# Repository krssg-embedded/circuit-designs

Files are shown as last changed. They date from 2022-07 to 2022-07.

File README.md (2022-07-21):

# Circuit Design
This repo contains all the schematics and pcb layout designs relevant to the SSL bot.
There are three imporatant circuits in the bot:
1. Main Board
2. Kicker Circuit
3. Motor Driver

### Main Board

### Kicker Circuit
The kicker we use works on the principle of a solenoid.
The straight kicker is powered by two 250V 2200uF capacitors, which can be charged by a step-up converter to 200V each.
The kicker board constitutes of a charging and a discharging circuit. The FPGA on the main circuit is controlling the circuit. The board receives charge trigger and kicking level from the main circuit, charging the capacitor bank of 4400uF to 250V using flyback topology.
The charging circuit is based on LT3750, a flyback converter. It consists of a different resistor which can be used to change various output parameters like charging current. The CHARGE pin one the IC gives full control of the LT3750 to the user and the DONE pin indicates when the capacitor has reached its programmed value, and the part has stopped charging.
The capacitor is charged to its limit by using a boost convertor that steps up the voltage from the the 12V battery. The kicker is operated through a switch which disconnects the charging circuit and allows the charge from the capacitor to flow through the solenoid. 
As the kicker is made of a magnetic material as soon as the current flows the coil tries to bring as much of the kicker inside itself as possible. This is what generates the tremendous kicking force required to kick the ball.

### Motor Driver
MOTOR DRIVER
In motor driver, I learnt how to make a commutation table.
I learnt in detail about the internal circuitry of the driver. I read about power MOSFETs and their advantages. We were taught the problems that we currently face in running our BLDCs. I learnt to place the components on the PCB and solder them properly. I also read about the gate driver IC we use and how it helps us in switching the states of the mosfets.
I read about the various methods of sensing commutation which includes using Hall sensors, using encoders and finally back-EMF calculations. The methods of control like trapezoidal, sinusoidal and field oriented control. The current sensor IC ACS2590 was also introduced. 
The main takeaway was that there are problems in the circuitry that we use and many things can be improved like we can implement sinusoidal current by applying variable PWM or make the commutation smoother by adjusting the rise and fall time of the voltages at the gates.

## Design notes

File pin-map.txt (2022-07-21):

3 Hall sensor per wheel motor -> 12 pins total (Interrupt)
6 output per motor     	      -> 15 pins total (PWM) + 15 pins total (digital)
4 output per Kicker           -> 4 pins total (digtal)
NRF Radio Communication	      -> 5 pins total (SPI)
Infrared Sensors              -> 3 pins total (digital)   
SWDIO, SWCLK (Programming)    -> 2 pin total (Serial Wire Debug)
ACS712 Current Feedback       -> 5 pin total (Analog)
2 input Encoder per motor     -> 8 pin total (Interrupt)
----------------------------------------------------------------
			      == 69 pins overall :P

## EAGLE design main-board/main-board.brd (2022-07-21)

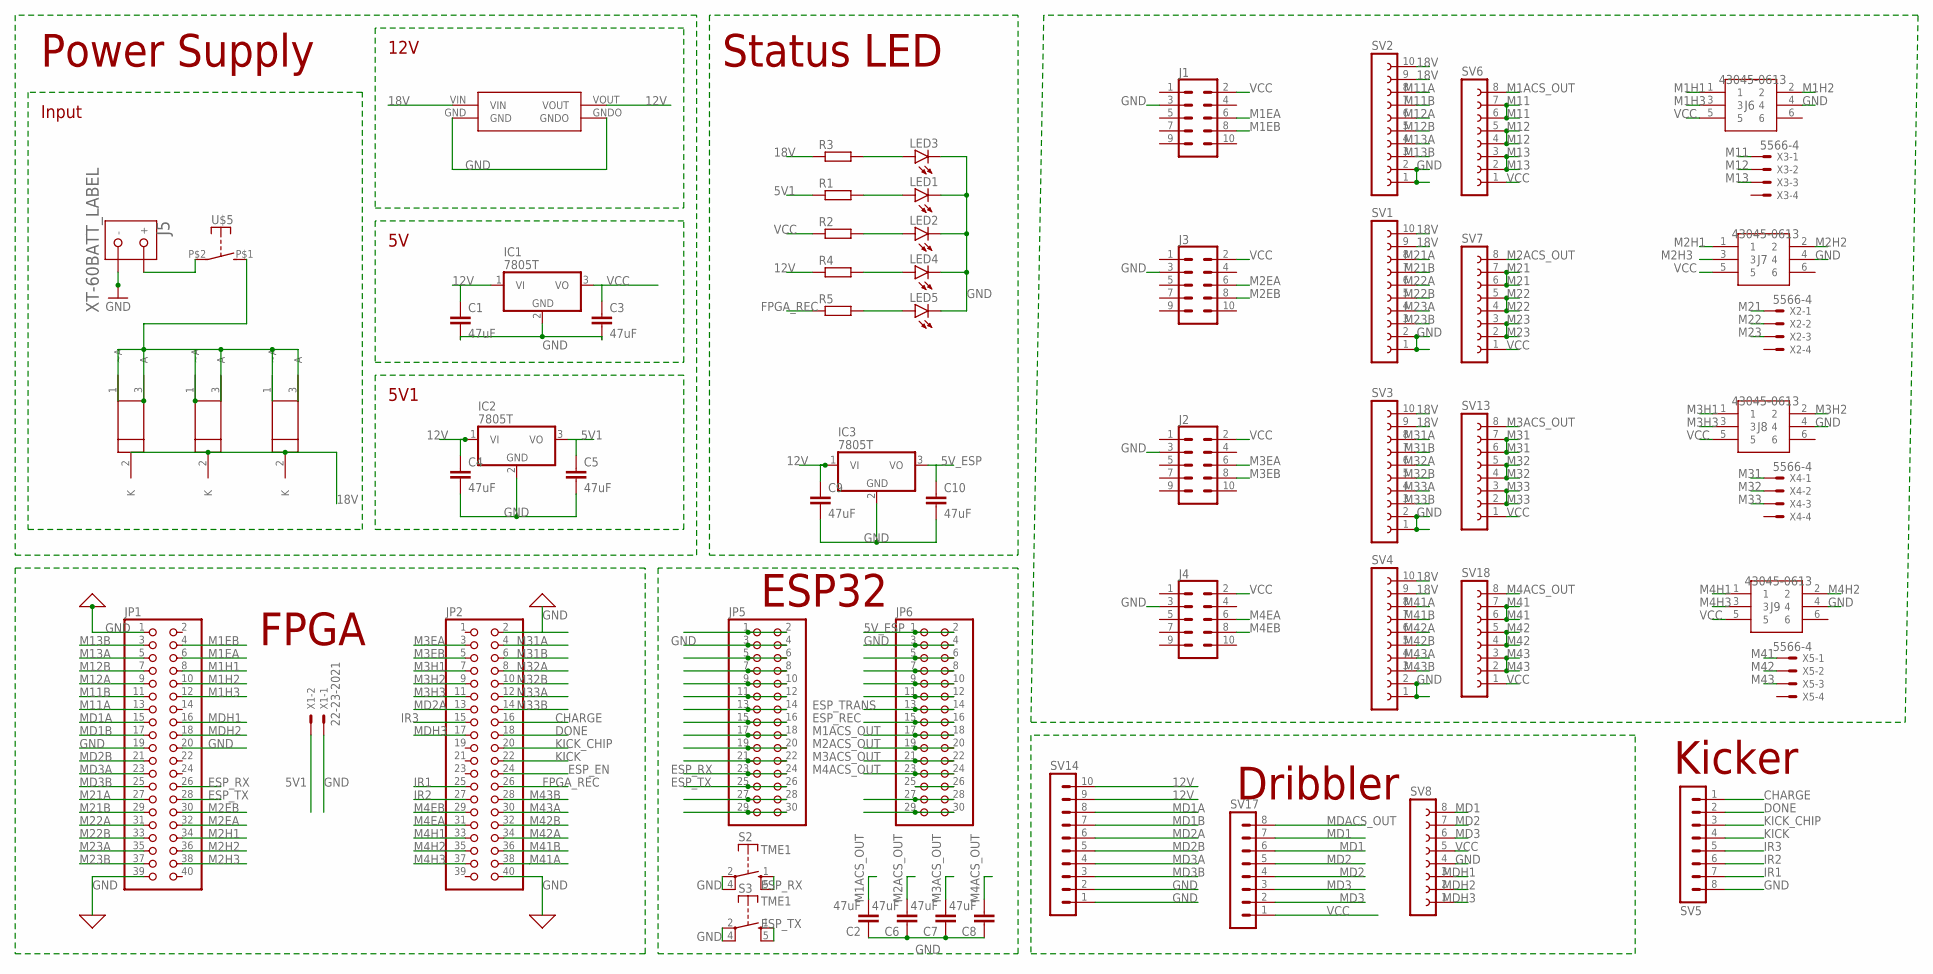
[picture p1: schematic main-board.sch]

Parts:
C1, C2, C3, C4, C5, C6, C7, C8, C9, C10: 47uF; C1206
IC1, IC2, IC3: 7805T; TO220H
J1, J2, J3, J4: CONN_05X2SHD_LOCK; 2X5-SHROUDED_LOCK
J5: XT-60BATT_LABEL; XT-60
J6, J7, J8, J9: 43045-0613
JP1, JP2: PINHD-2X20; 2X20
JP5, JP6: PINHD-2X15; 2X15
LED1, LED2, LED3, LED4, LED5: LEDSMT1206; 1206
R1, R2, R3, R4, R5: R-EU_R1206; R1206
S2, S3: TME1
SV1, SV2, SV3, SV4: FE10-1; FE10
SV5, SV17: MA08-1
SV6, SV7, SV8, SV13, SV18: FE08-1; FE08
SV14: MA10-1
U1, U2, U3: LP38690DT-3.3; TO228P1042X238-3N
U$4: BUCK
U$5: SWITCH_DA10; DA10
X1: 22-23-2021
X2, X3, X4, X5: 5566-4

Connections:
5V1: C5.1, IC2.3 (VO), R1.1, X1.2
5V_ESP: C10.1, IC3.3 (VO), JP6.1, JP6.2
12V: C1.1, C4.1, C9.1, IC1.1 (VI), IC2.1 (VI), IC3.1 (VI), R4.1, SV14.9, SV14.10, U$4.VOUT
18V: R3.1, SV1.9, SV1.10, SV2.9, SV2.10, SV3.9, SV3.10, SV4.9, SV4.10, U1.2 (K), U2.2 (K), U3.2 (K), U$4.VIN
CHARGE: JP2.16, SV5.1
DONE: JP2.18, SV5.2
ESP_EN: JP2.24
ESP_REC: JP6.15, JP6.16
ESP_RX: JP1.26, JP5.23, JP5.24, S2.1 (S), S2.5 (S)
ESP_TRANS: JP6.13, JP6.14
ESP_TX: JP1.28, JP5.25, JP5.26, S3.1 (S), S3.5 (S)
FPGA_REC: JP2.26, R5.1
GND: C1.2, C2.1, C3.2, C4.2, C5.2, C6.1, C7.1, C8.1, C9.2, C10.2, IC1.2 (GND), IC2.2 (GND), IC3.2 (GND), J1.3, J2.3, J3.3, J4.3, J5.GND (-), J6.4, J7.4, J8.4, J9.4, JP1.1, JP1.19, JP1.20, JP1.39, JP2.2, JP2.40, JP5.3, JP5.4, JP6.3, JP6.4, LED1.C, LED2.C, LED3.C, LED4.C, LED5.C, S2.2, S2.4, S3.2, S3.4, SV1.1, SV1.2, SV2.1, SV2.2, SV3.1, SV3.2, SV4.1, SV4.2, SV5.8, SV8.4, SV14.1, SV14.2, U$4.GND, U$4.GNDO, X1.1
INPUT: U1.1 (~A), U1.3 (A), U2.1 (~A), U2.3 (A), U3.1 (~A), U3.3 (A), U$5.P$1 (S)
IR1: JP2.25, SV5.7
IR2: JP2.27, SV5.6
IR3: JP2.15, SV5.5
KICK: JP2.22, SV5.4
KICK_CHIP: JP2.20, SV5.3
M1ACS_OUT: C2.2, JP6.17, JP6.18, SV6.8
M1EA: J1.6, JP1.6
M1EB: J1.8, JP1.4
M1H1: J6.1, JP1.8
M1H2: J6.2, JP1.10
M1H3: J6.3, JP1.12
M2ACS_OUT: C6.2, JP6.19, JP6.20, SV7.8
M2EA: J3.6, JP1.32
M2EB: J3.8, JP1.30
M2H1: J7.1, JP1.34
M2H2: J7.2, JP1.36
M2H3: J7.3, JP1.38
M3ACS_OUT: C7.2, JP6.21, JP6.22, SV13.8
M3EA: J2.6, JP2.3
M3EB: J2.8, JP2.5
M3H1: J8.1, JP2.7
M3H2: J8.2, JP2.9
M3H3: J8.3, JP2.11
M4ACS_OUT: C8.2, JP6.23, JP6.24, SV18.8
M4EA: J4.6, JP2.31
M4EB: J4.8, JP2.29
M4H1: J9.1, JP2.33
M4H2: J9.2, JP2.35
M4H3: J9.3, JP2.37
M11: SV6.6, SV6.7, X3.1
M11A: JP1.13, SV2.8
M11B: JP1.11, SV2.7
M12: SV6.4, SV6.5, X3.2
M12A: JP1.9, SV2.6
M12B: JP1.7, SV2.5
M13: SV6.2, SV6.3, X3.3
M13A: JP1.5, SV2.4
M13B: JP1.3, SV2.3
M21: SV7.6, SV7.7, X2.1
M21A: JP1.27, SV1.8
M21B: JP1.29, SV1.7
M22: SV7.4, SV7.5, X2.2
M22A: JP1.31, SV1.6
M22B: JP1.33, SV1.5
M23: SV7.2, SV7.3, X2.3
M23A: JP1.35, SV1.4
M23B: JP1.37, SV1.3
M31: SV13.6, SV13.7, X4.1
M31A: JP2.4, SV3.8
M31B: JP2.6, SV3.7
M32: SV13.4, SV13.5, X4.2
M32A: JP2.8, SV3.6
M32B: JP2.10, SV3.5
M33: SV13.2, SV13.3, X4.3
M33A: JP2.12, SV3.4
M33B: JP2.14, SV3.3
M41: SV18.6, SV18.7, X5.1
M41A: JP2.38, SV4.8
M41B: JP2.36, SV4.7
M42: SV18.4, SV18.5, X5.2
M42A: JP2.34, SV4.6
M42B: JP2.32, SV4.5
M43: SV18.2, SV18.3, X5.3
M43A: JP2.30, SV4.4
M43B: JP2.28, SV4.3
MD1: SV8.8, SV17.6, SV17.7
MD1A: JP1.15, SV14.8
MD1B: JP1.17, SV14.7
MD2: SV8.7, SV17.4, SV17.5
MD2A: JP2.13, SV14.6
MD2B: JP1.21, SV14.5
MD3: SV8.6, SV17.2, SV17.3
MD3A: JP1.23, SV14.4
MD3B: JP1.25, SV14.3
MDACS_OUT: SV17.8
MDH1: JP1.16, SV8.3
MDH2: JP1.18, SV8.2
MDH3: JP2.17, SV8.1
unnamed: JP5.1, JP5.2
unnamed: LED1.A, R1.2
unnamed: JP5.5, JP5.6
unnamed: LED2.A, R2.2
unnamed: JP5.7, JP5.8
unnamed: JP5.9, JP5.10
unnamed: LED3.A, R3.2
unnamed: JP5.11, JP5.12
unnamed: JP5.13, JP5.14
unnamed: LED4.A, R4.2
unnamed: JP5.15, JP5.16
unnamed: JP5.17, JP5.18
unnamed: LED5.A, R5.2
unnamed: JP5.19, JP5.20
unnamed: JP5.21, JP5.22
unnamed: JP5.27, JP5.28
unnamed: JP5.29, JP5.30
unnamed: JP6.5, JP6.6
unnamed: JP6.7, JP6.8
unnamed: JP6.9, JP6.10
unnamed: JP6.11, JP6.12
unnamed: JP6.27, JP6.28
unnamed: JP6.29, JP6.30
unnamed: JP6.25, JP6.26
SUPP: J5.BATT (+), U$5.P$2
VCC: C3.1, IC1.3 (VO), J1.2, J2.2, J3.2, J4.2, J6.5, J7.5, J8.5, J9.5, R2.1, SV6.1, SV7.1, SV8.5, SV13.1, SV17.1, SV18.1

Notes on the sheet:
Power Supply
FPGA
Status LED
Dribbler
Kicker
ESP32
Input
12V
5V1

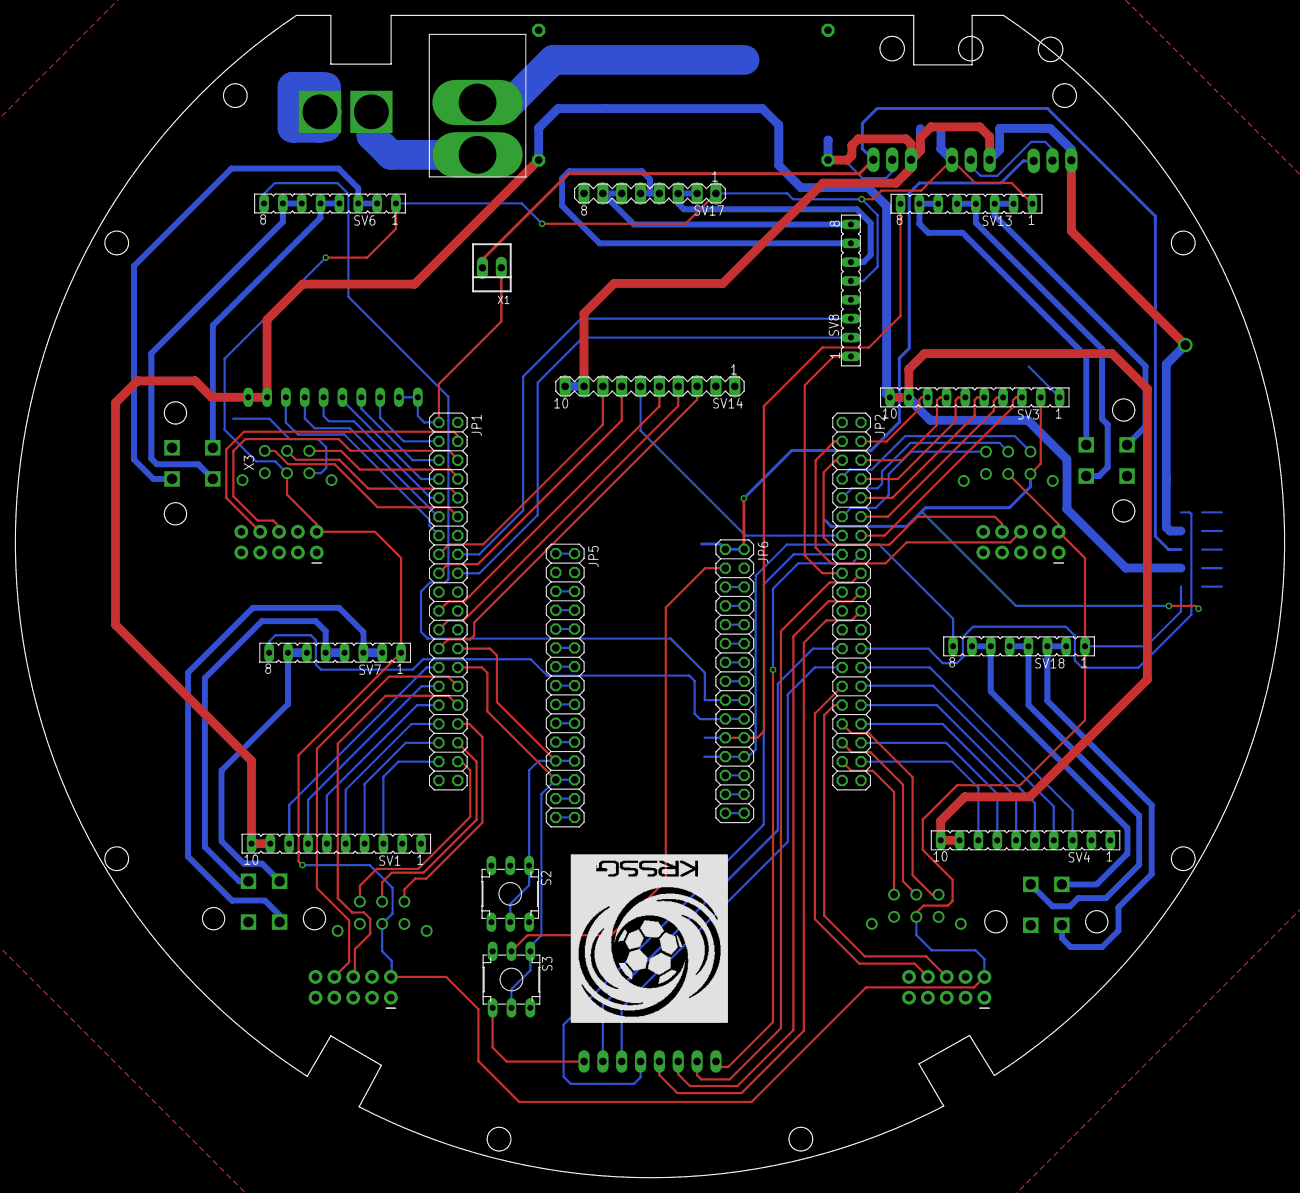
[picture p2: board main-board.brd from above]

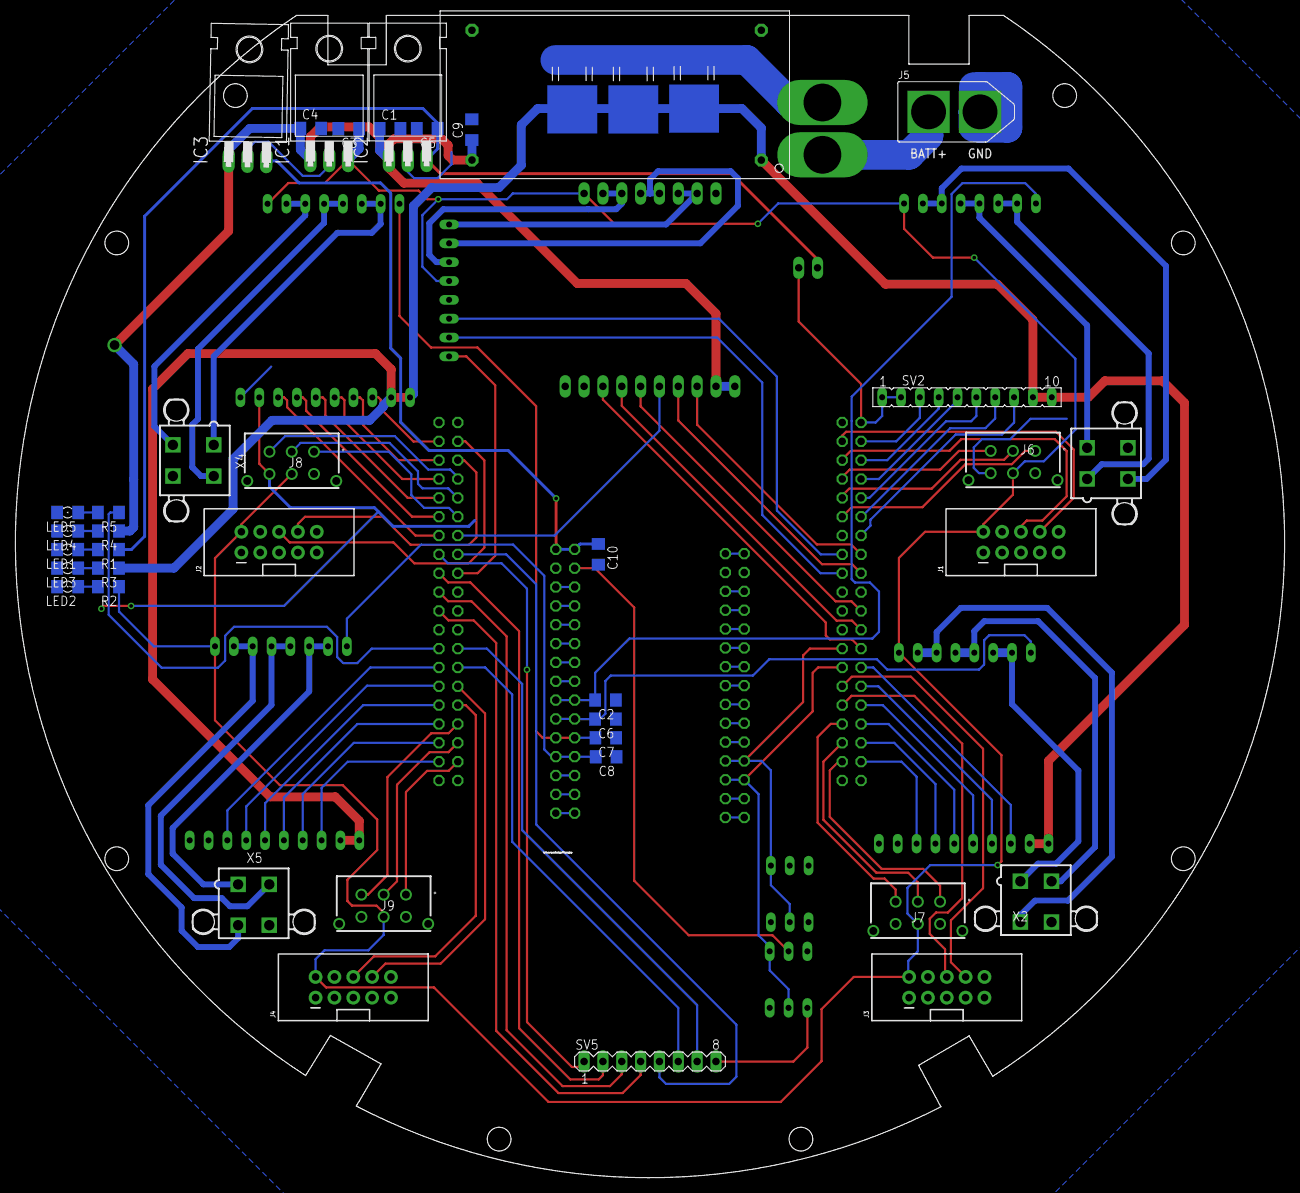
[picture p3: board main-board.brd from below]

Board: 2 copper layers, 171.1 x 156.7 mm, 61 parts (42 on the bottom side), 116 nets.

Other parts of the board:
U$1: LOGO3

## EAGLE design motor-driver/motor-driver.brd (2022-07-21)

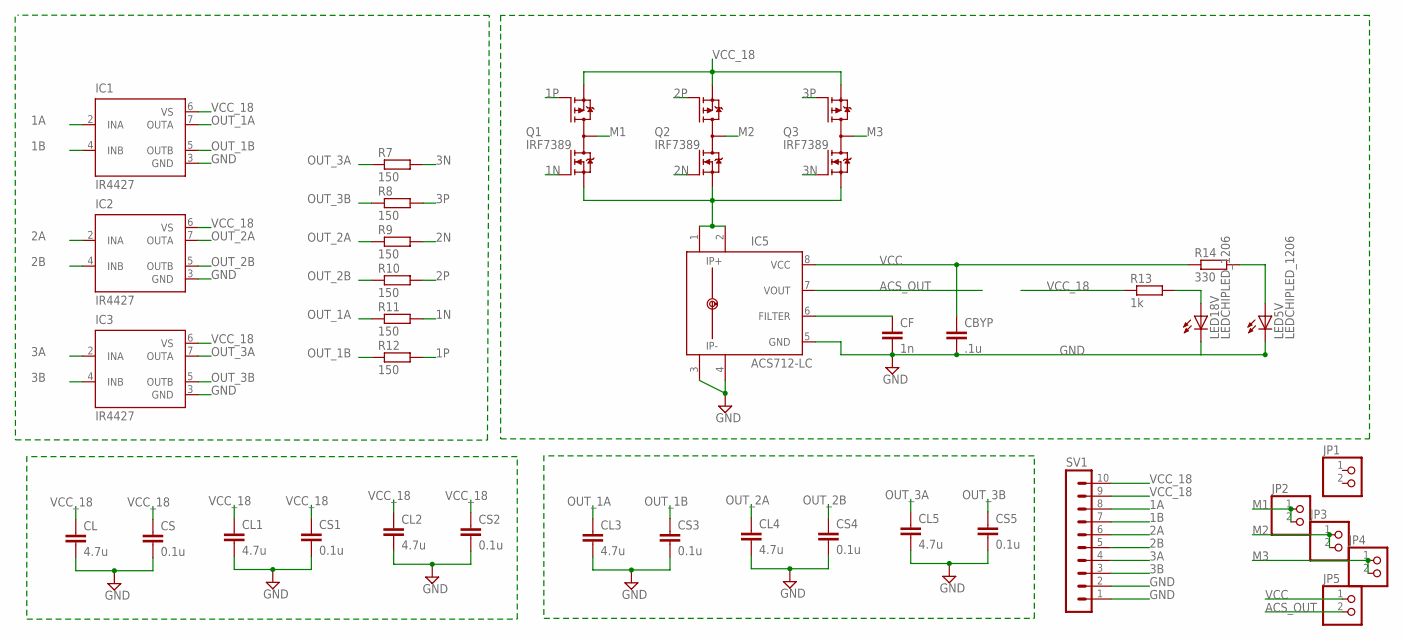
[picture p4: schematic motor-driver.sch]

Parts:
CBYP: .1u; C1206
CF: 1n; C1206
CL, CL1, CL2, CL3, CL4, CL5: 4.7u; C1206
CS, CS1, CS2, CS3, CS4, CS5: 0.1u; C1206
IC1, IC2, IC3: IR4427; DIL08
IC5: ACS712-LC; SOIC8
JP1, JP2, JP3, JP4, JP5: PINHD-1X2; 1X02
LED5V, LED18V: LEDCHIPLED_1206; CHIPLED_1206
Q1, Q2, Q3: IRF7389; SO08-IRF
R7, R8, R9, R10, R11, R12: 150; R1206
R13: 1k; R1206
R14: 330; R1206
SV1: MA10-1

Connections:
1A: IC1.2 (INA), SV1.8
1B: IC1.4 (INB), SV1.7
1N: Q1.2 (N-G), R11.2
1P: Q1.4 (P-G), R12.2
2A: IC2.2 (INA), SV1.6
2B: IC2.4 (INB), SV1.5
2N: Q2.2 (N-G), R9.2
2P: Q2.4 (P-G), R10.2
3A: IC3.2 (INA), SV1.4
3B: IC3.4 (INB), SV1.3
3N: Q3.2 (N-G), R7.2
3P: Q3.4 (P-G), R8.2
ACS_OUT: IC5.7 (VOUT), JP5.2
FILTER_ACS: CF.1, IC5.6 (FILTER)
GND: CBYP.2, CF.2, CL.2, CL1.2, CL2.2, CL3.2, CL4.2, CL5.2, CS.2, CS1.2, CS2.2, CS3.2, CS4.2, CS5.2, IC1.3 (GND), IC2.3 (GND), IC3.3 (GND), IC5.3 (IP-), IC5.4 (IP-1), IC5.5 (GND), LED5V.C, LED18V.C, SV1.1, SV1.2
M1: JP2.1, JP2.2, Q1.5 (D), Q1.6 (D), Q1.7 (D), Q1.8 (D)
M2: JP3.1, JP3.2, Q2.5 (D), Q2.6 (D), Q2.7 (D), Q2.8 (D)
M3: JP4.1, JP4.2, Q3.5 (D), Q3.6 (D), Q3.7 (D), Q3.8 (D)
unnamed: LED18V.A, R13.2
unnamed: LED5V.A, R14.2
OUT_1A: CL3.1, IC1.7 (OUTA), R11.1
OUT_1B: CS3.1, IC1.5 (OUTB), R12.1
OUT_2A: CL4.1, IC2.7 (OUTA), R9.1
OUT_2B: CS4.1, IC2.5 (OUTB), R10.1
OUT_3A: CL5.1, IC3.7 (OUTA), R7.1
OUT_3B: CS5.1, IC3.5 (OUTB), R8.1
SINK: IC5.1 (IP+), IC5.2 (IP+1), Q1.1 (N-S), Q2.1 (N-S), Q3.1 (N-S)
VCC: CBYP.1, IC5.8 (VCC), JP5.1, R14.1
VCC_18: CL.1, CL1.1, CL2.1, CS.1, CS1.1, CS2.1, IC1.6 (VS), IC2.6 (VS), IC3.6 (VS), Q1.3 (P-S), Q2.3 (P-S), Q3.3 (P-S), R13.1, SV1.9, SV1.10

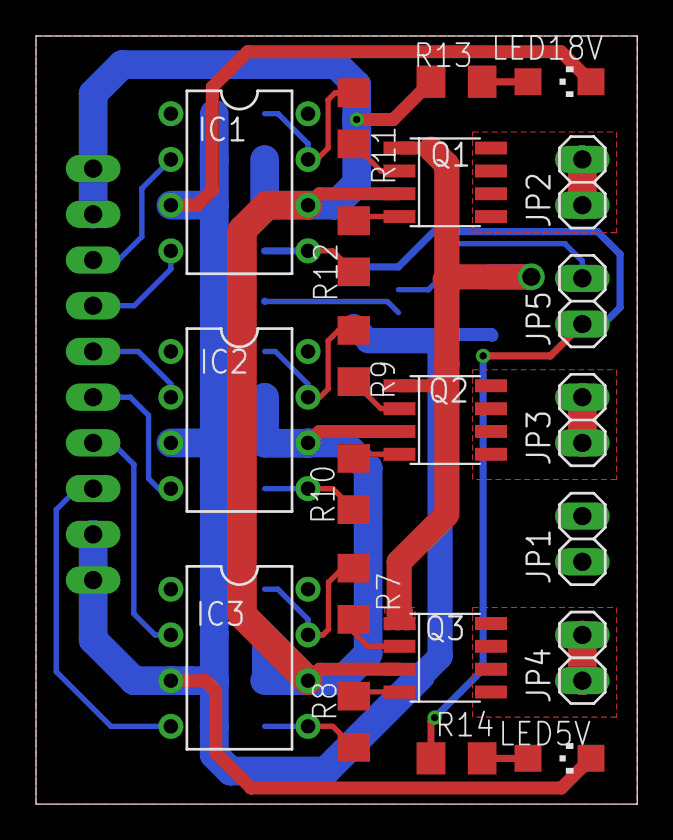
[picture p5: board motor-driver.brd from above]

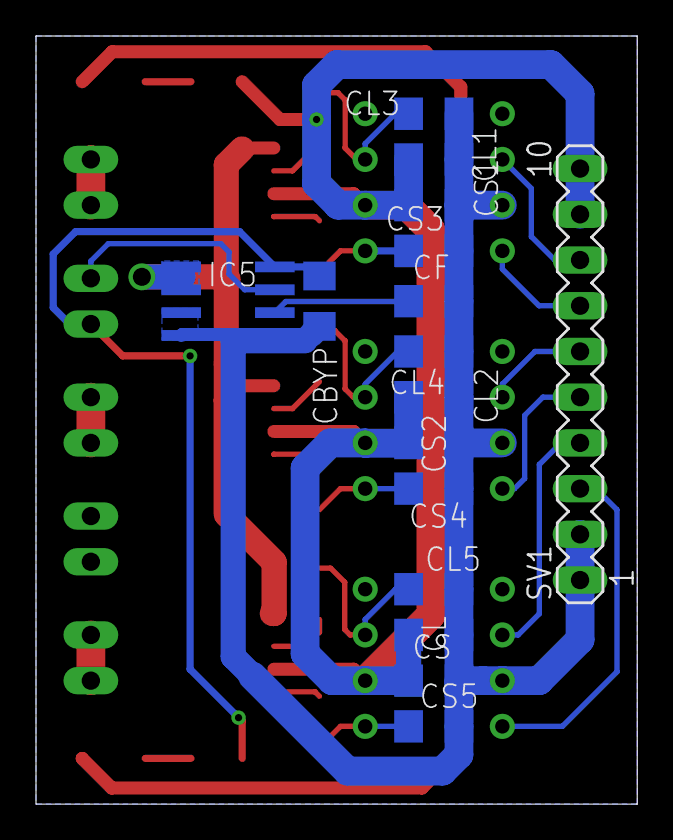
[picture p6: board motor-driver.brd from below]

Board: 2 copper layers, 33.4 x 42.7 mm, 37 parts (16 on the bottom side), 29 nets.

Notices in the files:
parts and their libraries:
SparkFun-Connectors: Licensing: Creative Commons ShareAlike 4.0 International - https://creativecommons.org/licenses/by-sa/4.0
